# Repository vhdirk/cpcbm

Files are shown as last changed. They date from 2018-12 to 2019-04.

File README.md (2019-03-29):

## NOTE: All the files and informations in the mechanics folder of this repository are licensed under CC-BY-NC-SA license.

## Please, refer to the following link to know the details about this license.



## News[31-12-2018]: The complete release of the mechanical drawings of the machine are OUT!!! Informative videos will follow as soon as possible.

## Youtube Channel: [The Ant PCB Maker](https://www.youtube.com/channel/UCX44z-SSL7LzcB4xxgUdHHA)

## Instagram : [The Ant Team](https://www.instagram.com/the_ant_team/)

## Contact us at: the.ant.pcb@gmail.com or compact.pcb.maker.team@gmail.com

alternativetext (https://www.youtube.com/channel/UCX44z-SSL7LzcB4xxgUdHHA)

The Ant is a project to develop a CNC machine able to realize single and double-layered printed circuit boards.

[Here is a video presentation](https://youtu.be/nVkbG-CYaAA)

The CNC machine is designed to achieve well-determined characteristics:

- Compact
- Low-cost
- Robust
- Scalable
- Easy to build
- Open License

To achieve these properties the following design principle have been adopted:

- Electrical, mechanical and electronics parts have been chosen to be small, low-cost and easily available on the open market or 3D printable
- Mechanical design has been oriented to minimize the space occupied by the components
- Mechanics has been designed to be robust and stress resistant
- Mechanics has been designed so that the external dimensions of the machine may be changed with a minimal change of pieces and no re-design needed.
- Mechanical and electrical designs have taken in account the assembling and disassembling operations, allowing to use easily available tools as screwdrivers, Allen wrenches and a solder for electrical contacts.
- The microcontroller board used to control the CNC machine is inexpensive (~15 $) but is equipped with a powerful STM32 processor and many peripherals.
- The machine control firmware can be loaded with almost no effort, since the microcontroller board has been chosen to have an on-board programmer.
- The control firmware is derived from GRBL v.0.9j, but it is also customized to achieve better performance, taking advantage of the powerful processor, and to be more flexible, since more configuration parameters and features have been added respect to the original firmware

The Ant is an open project, but if you feel like donating a small sum, you are very welcome. Just use the paypal button below.

paypal (https://www.paypal.com/cgi-bin/webscr?cmd=_s-xclick&hosted_button_id=BTRCVPZUZYW2E)

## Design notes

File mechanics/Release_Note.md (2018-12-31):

# 31-12-2018

## Scope

Release of mechanical drawings of the Compact PCB Maker. 
This release completes the previous one and comprises the mechanical drawings of the bridge, of the head and of the microcontroller cover. 
The suggestions of the previous release apply also to this one.

# 09-12-2018

## Scope

First release of mechanical drawings of the Compact PCB Maker. 
This is a partial release that comprises all the frame related mechanical drawings. Other parts and corrections will follow in other releases.

## Suggestions

We suggest you to print the parts as they are, because the printing position is designed to enhance the mechanical behavior.

We also suggest you to print with a 0.2 mm layer thickness, 25% of infill, 1.5 mm of wall thickness and extrusion width (also called line width) of 0.5 mm.

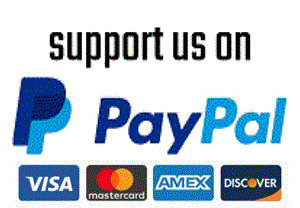
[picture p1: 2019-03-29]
resources/button/pp_button_small.gif

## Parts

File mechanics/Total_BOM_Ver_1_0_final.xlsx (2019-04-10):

Item | 1 | 2 | 3 | 4 | 5 | 6 | Qty | Info
Makerbeam - 10x10mm aluminum profile 200mm (black) | 8 |  |  |  |  |  | 8 | Makerbeam
Makerbeam - 10x10mm aluminum profile 60mm (black) | 4 |  |  |  |  |  | 4 | Makerbeam
Makerbeam - 10x10mm aluminum Right Angle bracket | 8 |  |  |  |  |  | 8 | Makerbeam
M3x6mm square headed bolt | 47 |  |  |  |  |  | 47 | Makerbeam
ISO 7380 M3X4 A2 | 8 |  |  |  | 4 |  | 12 | Makerbeam
Makerbeam T-slot nut | 24 |  |  |  |  |  | 24 | Makerbeam
M3 self-locking nut | 46 | 9 |  | 2 |  |  | 57
M3 nut | 4 |  |  |  |  | 8 | 12
M5 nut |  |  |  | 1 |  | 2 | 3
M2x8mm DIN 912 bolt |  |  |  |  | 2 |  | 2
M2.5x8mm DIN 912 bolt |  |  |  | 8 |  |  | 8
M3x6mm DIN 912 bolt | 12 | 9 |  | 2 | 3 |  | 26
M3x8mm DIN 912 bolt |  |  |  |  | 4 |  | 4
M3x10mm DIN 912 bolt |  | 4 |  |  |  | 8 | 12
M3x16mm DIN 912 Bolt | 2 |  |  |  | 4 |  | 6
M3x20mm DIN 912 Bolt | 8 |  |  | 1 |  |  | 9
M3x25mm DIN 912 bolt |  |  |  | 2 |  |  | 2
M3x30mm DIN 912 Bolt | 4 |  |  |  |  |  | 4
M3x50mm DIN 912 bolt |  | 2 |  |  | 4 |  | 6
M5x16mm hexagon head bolt |  |  |  |  |  | 2 | 2
Wood screws 3x16mm |  |  |  |  |  | 6 | 6
M3 locking Washer (internal diameter 3mm, external 5.5mm) | 8 | 14 |  |  |  |  | 22
M3 Washer (internal diameter 3mm, external 7.5mm) | 16 | 10 |  |  |  |  | 26
GT2 pulley 16T Bore 3mm with bearings | 4 | 2 |  |  |  |  | 6 | Aliexpress
GT2 pulley No Teeth Bore 3mm with bearings |  | 2 |  |  |  |  | 2 | Aliexpress
GT2 pulley 16T Bore 5mm height 10mm |  |  |  | 2 |  |  | 2 | Aliexpress
GT2 6mm Timing belt piece 100 cm |  |  |  | 2 |  |  | 2 | Aliexpress
Timing Belt Tensioner Spring | 2 |  |  |  |  |  | 2 | SKU135539-3 FFIO PCK
MGN9H Linear Rail 200 mm | 2 |  |  |  |  |  | 2 | Aliexpress or Banggood
Bearings lm6uu |  | 8 |  |  |  |  | 8 | Amazon
Bearing mochu 706C |  | 2 |  |  |  |  | 2 | Aliexpress
Chrome Plated Rods 6x180mm |  | 2 |  |  |  |  | 2 | Aliexpress (can be 6x200mm)
Chrome Plated Rods 6x100mm |  | 2 |  |  |  |  | 2
Threaded Rods M3x100mm |  | 3 |  |  |  |  | 3
Mechanical Limit Switch Module Vertical |  | 2 |  |  |  |  | 2 | Aliexpress
Mechanical endstop micro switch with dupont terminal |  |  | 1 |  |  |  | 1 | Aliexpress
ER8M-C6-60L chuck with 1/8" spring collect |  |  |  | 1 |  |  | 1 | Aliexpress
Lock collar(ring) internal diameter 6 mm, external diameter 12mm |  |  |  | 1 |  |  | 1 | Amazon or Aliexpress. The measured external diameter is 13mm
O-ring inner diameter 17mm, 1.78mm thick |  |  |  |  |  | 2 | 2
NEMA-11 JK28HS51-674 |  |  | 2 |  |  |  | 2 | Aliexpress or Banggood
Z axis motor LC1574W-04-025 |  |  |  | 1 |  |  | 1
M12 nut with step 1.75mm, 5mm thick |  |  |  | 1 |  |  | 1 | This should be sold with the Z-axis motor, if not use the correspondant 3D printed part.
2632 brushless outrunner motor 1000 kV |  |  | 1 |  |  |  | 1 | Turnigy on HobbyKing or Mistery on Aliexpress. The latter is still not tested and requires different head pieces
ESC AFRO 20A |  |  | 1 |  |  |  | 1 | HobbyKing
Nucleo F401RE |  |  |  |  | 1 |  | 1
CNC arduino shield V3 |  |  |  |  | 1 |  | 1
Stepstick stepper driver |  |  |  |  | 3 |  | 3
Male 3.5 bullet connectors |  |  | 3 |  |  |  | 3
Female 3.5mm bullet connectors |  |  | 2 |  |  |  | 2
Male JST connector |  |  | 1 |  |  |  | 1
Female Dupont connector 1x04 |  |  | 2 |  |  |  | 2
Female Dupont pin |  |  | 14 |  |  |  | 14
Female Dupont connector 1x03 |  |  | 2 |  |  |  | 2
Crocodile clips with plastic covers |  |  | 2 |  |  |  | 2
Extension Servo Lead Wire Male to Female 10 cm cable |  |  | 1 |  |  |  | 1
Stereo earphone with jack 3.5mm |  |  | 1 |  |  |  | 1
Cable 26 AWG about 40 cm |  |  | 4 |  |  |  | 4
Cable 16 AWG about 40 cm |  |  | 2 |  |  |  | 2
Cable 16AWG about 20cm |  |  |  |  | 2 |  | 2
Dupont cable Female to Female 20 cm |  |  |  |  | 2 |  | 2
Pieces of heat shrink tube |  |  |  |  |  |  |  | Various with different sizes
Small zip ties |  |  |  | 4 |  |  | 4
2.54mm jumper |  |  |  |  | 10 |  | 10
Sheath spiral tube 6 mm about 1 m |  |  |  |  | 1 |  | 1
MDF wood board 240x150x10mm (LxWxH) |  |  |  | 1 |  |  | 1
12V on-off round switch with 14mm mounting hole |  |  |  |  | 1 |  | 1
Panel mount DC power jack inner diameter 2.5mm external diameter 5.5mm |  |  |  |  | 1 |  | 1
Panel mount 3.5mm mono female headphone plug |  |  |  |  | 1 |  | 1
12V brushless 40x40x10mm fan |  |  |  |  | 1 |  | 1
12V 10A power supply |  |  |  |  |  | 1 | 1

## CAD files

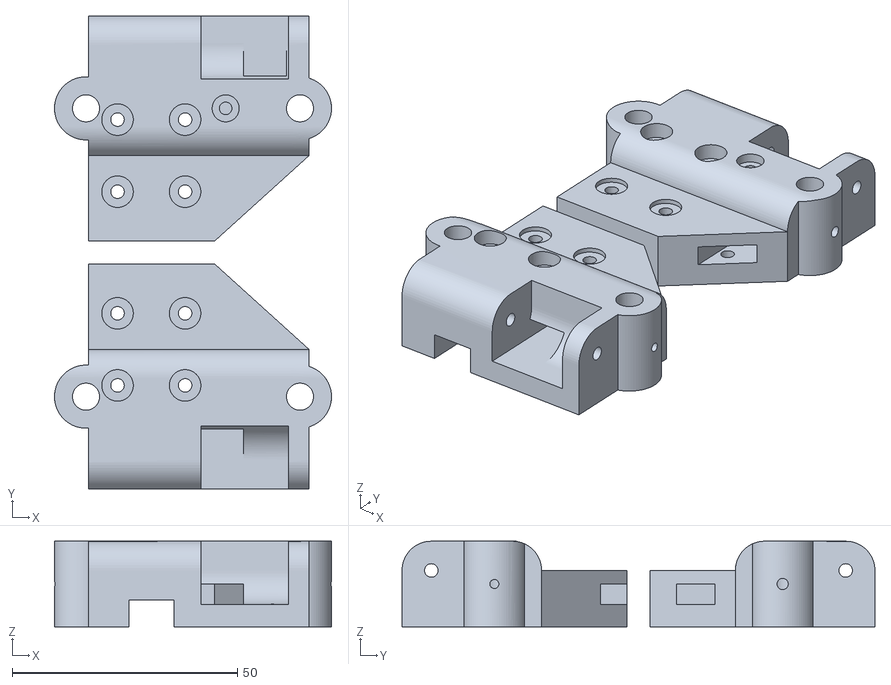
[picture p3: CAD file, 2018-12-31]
mechanics/bridge/bridge_right_and_left_1p2.stl
61.5 x 105.0 x 19.0

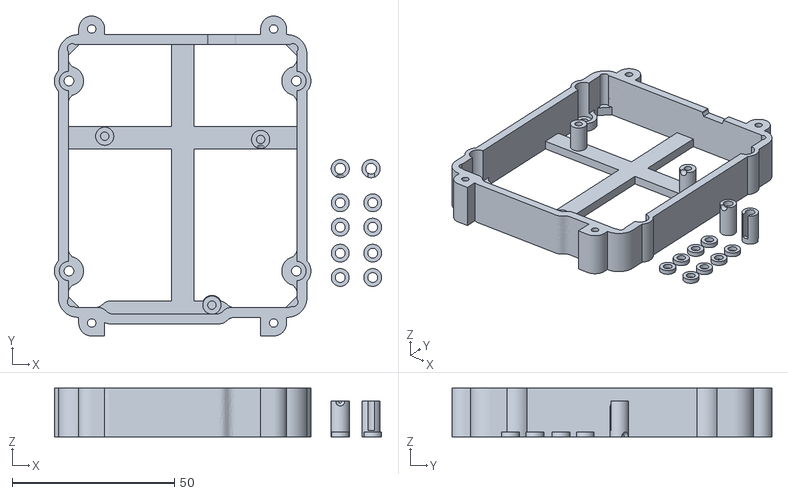
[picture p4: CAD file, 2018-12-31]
mechanics/electronics_and_accessories/nucleo_back_1p4.stl
100.8 x 98.5 x 15.0

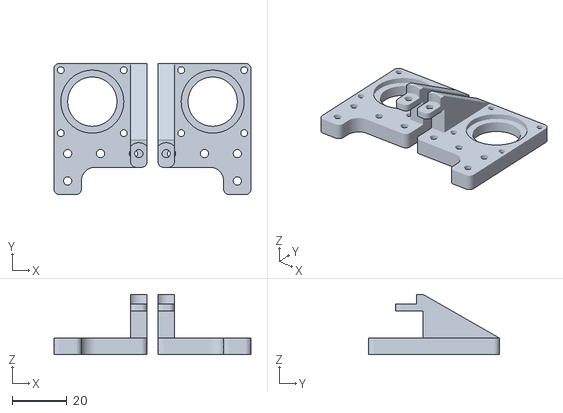
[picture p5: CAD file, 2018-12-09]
mechanics/frame/motor_holder_1p0.stl
72.0 x 48.0 x 22.0

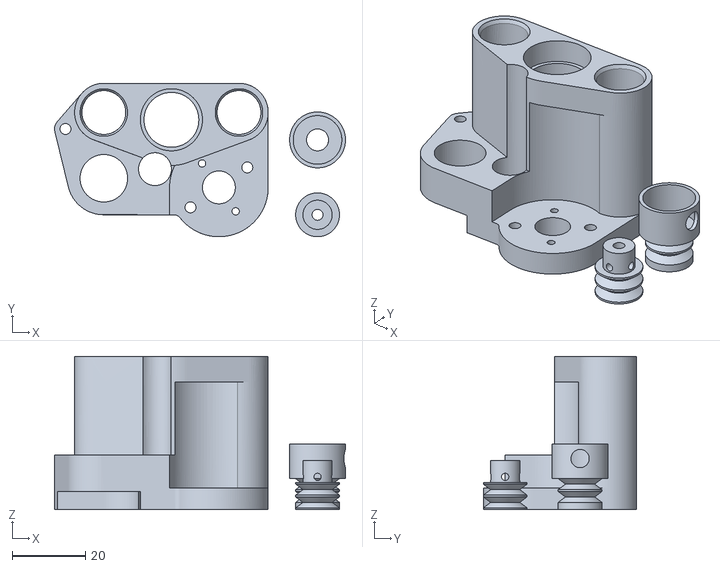
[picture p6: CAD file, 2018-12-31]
mechanics/head/head_4p0.stl
79.7 x 42.0 x 42.0

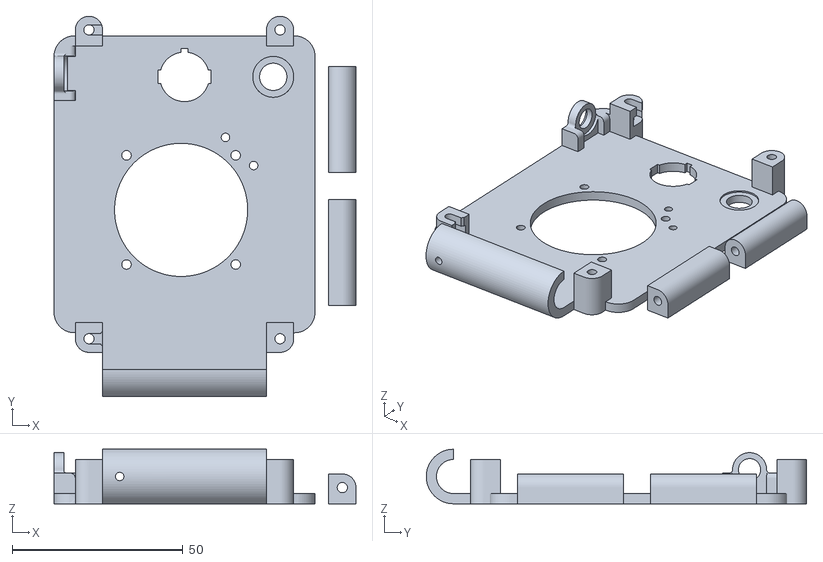
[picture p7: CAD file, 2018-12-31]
mechanics/electronics_and_accessories/nucleo_cover_1p4.stl
88.5 x 111.5 x 16.0

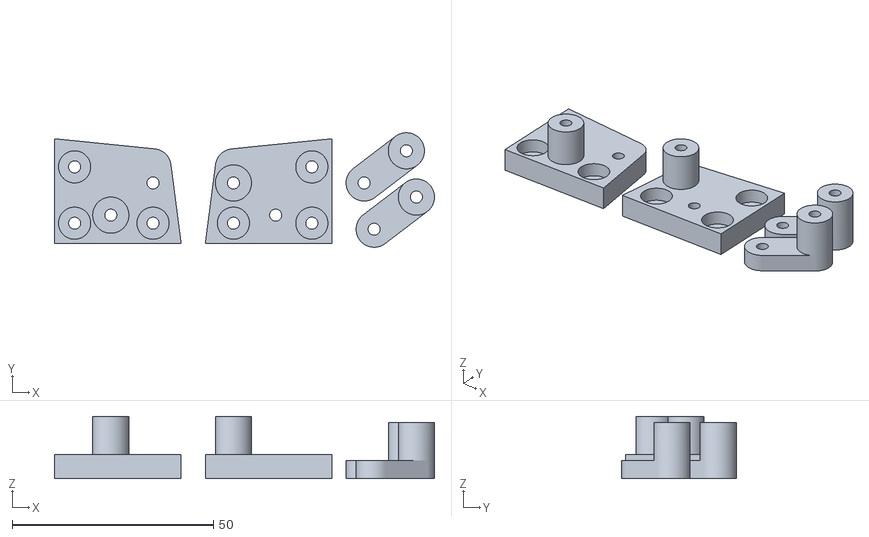
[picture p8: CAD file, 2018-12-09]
mechanics/frame/GT2_pulley_support_1p0.stl
94.5 x 28.5 x 15.5

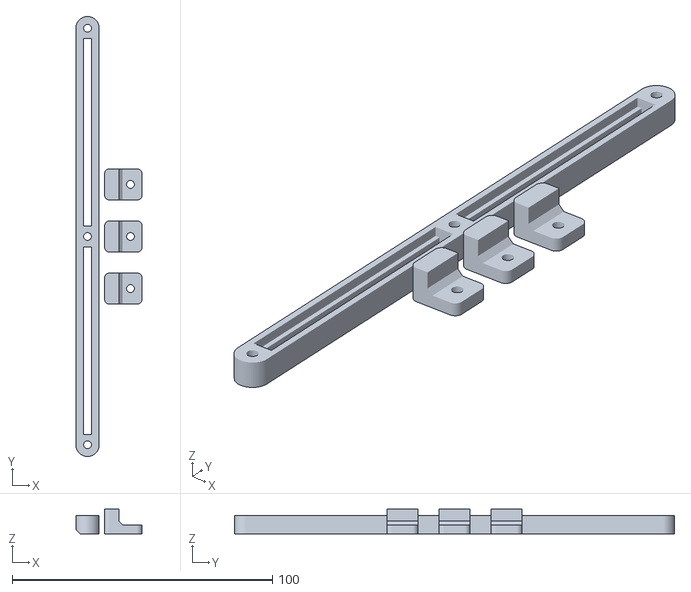
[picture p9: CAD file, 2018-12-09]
mechanics/frame/pcb_lock_1p0.stl
25.5 x 169.0 x 9.50

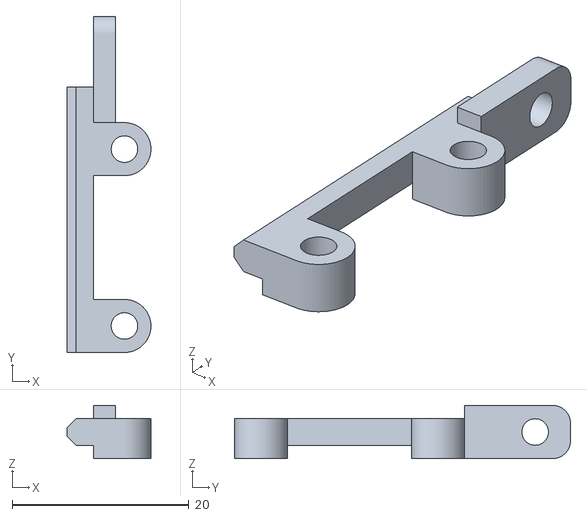
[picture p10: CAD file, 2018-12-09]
mechanics/frame/limit_y_support_1p0.stl
9.50 x 38.0 x 6.00

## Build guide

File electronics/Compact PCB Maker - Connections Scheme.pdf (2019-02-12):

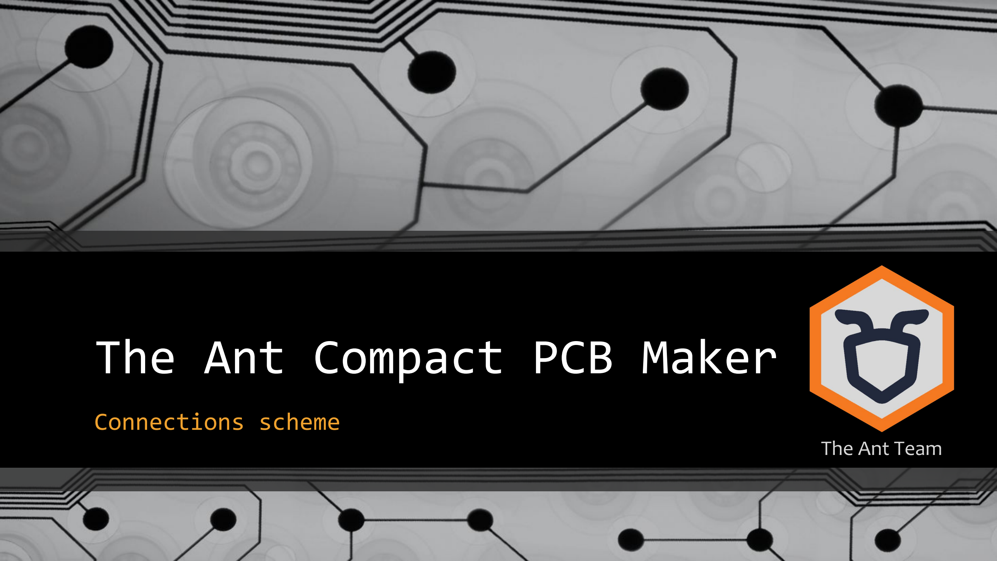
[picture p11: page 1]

# The Ant Compact PCB Maker

### Connections scheme

The Ant Team

# Introduction

## This document shows how to connect the different electronics parts of The Ant Machine. We strongly suggests you to watch this video:

## https://youtu.be/eRefCvD_KVs

as a preparation for this stage of machine construction.

# Electronics central unit parts

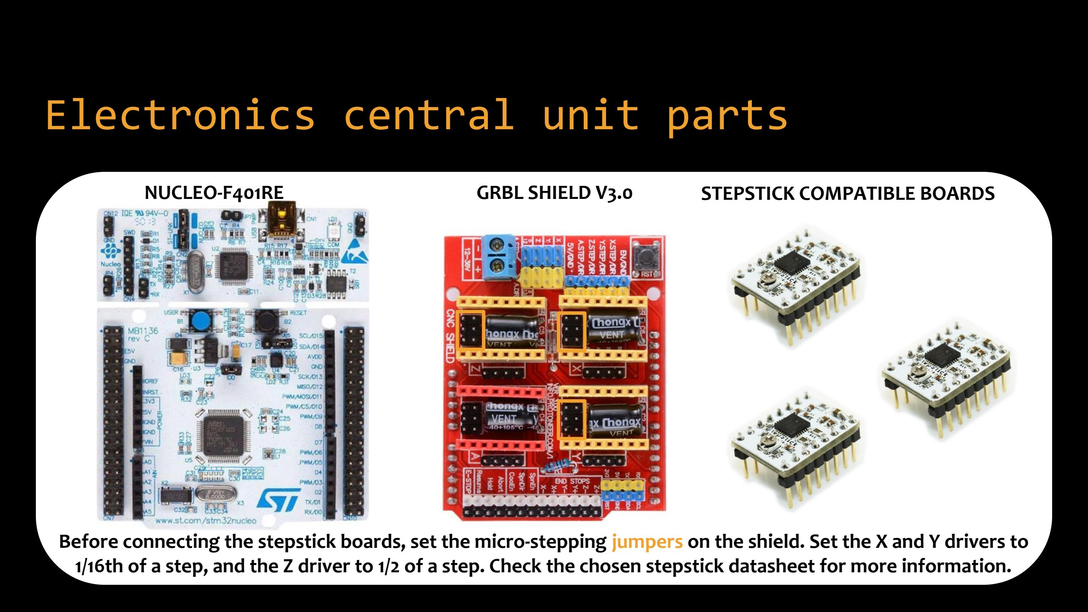
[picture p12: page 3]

Before connecting the stepstick boards, set the micro-stepping jumpers on the shield. Set the X and Y drivers to 1/16th of a step, and the Z driver to 1/2 of a step. Check the chosen stepstick datasheet for more information.

NUCLEO-F401RE | GRBL SHIELD V3.0 | STEPSTICK COMPATIBLE BOARDS

# Power Supply

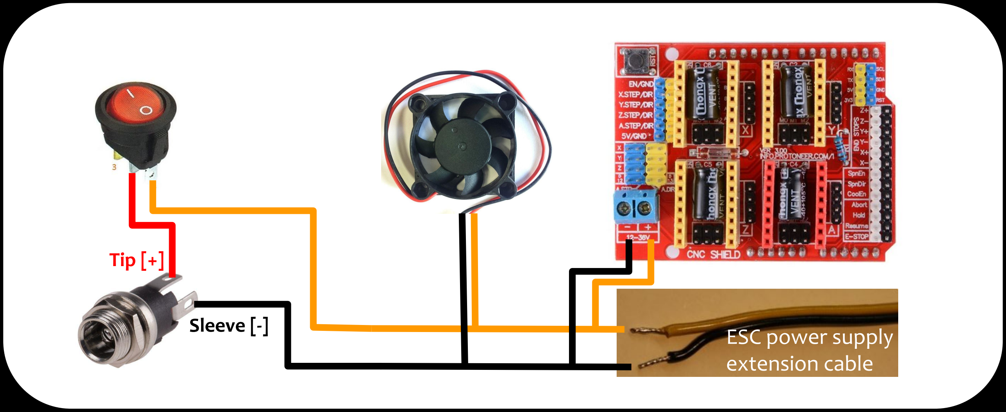
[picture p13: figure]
ESC power supply extension cable; Sleeve [-]; Tip [+]

# ESC Power Supply

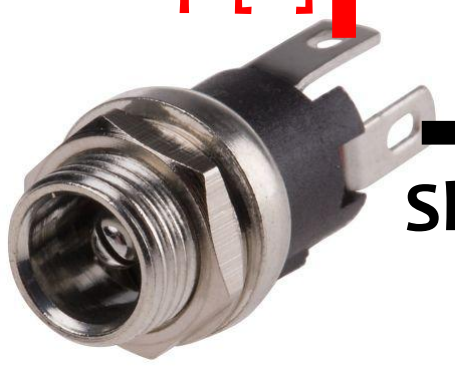
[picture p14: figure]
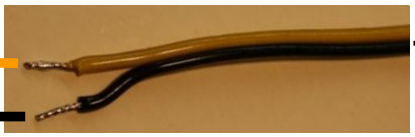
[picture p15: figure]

Sleeve [-]

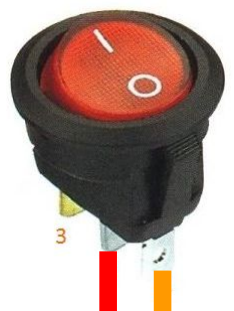
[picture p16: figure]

Tip [+]

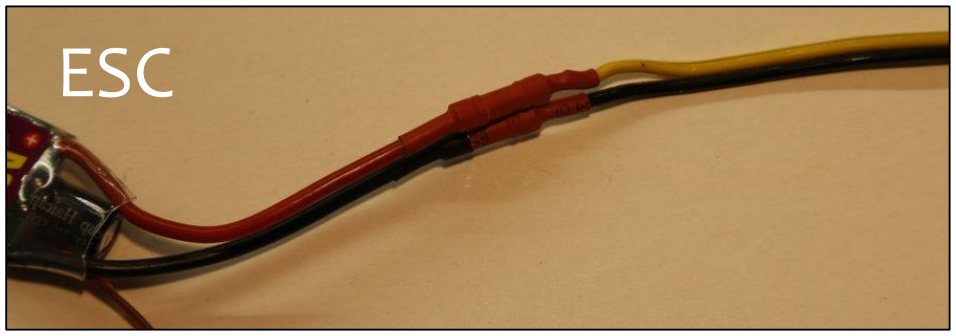
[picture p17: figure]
ESC

# CoreXY Stepper Motors

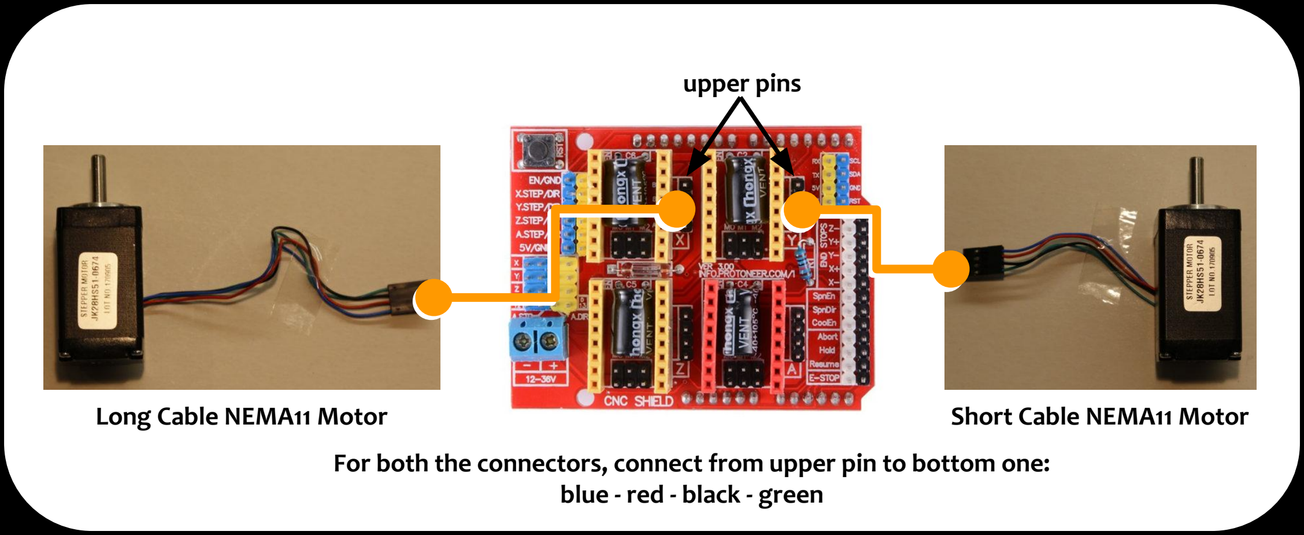
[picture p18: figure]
blue - red - black - green; upper pins; Long Cable NEMA11 Motor; Short Cable NEMA11 Motor

For both the connectors, connect from upper pin to bottom one:

# Z axis Stepper Motor

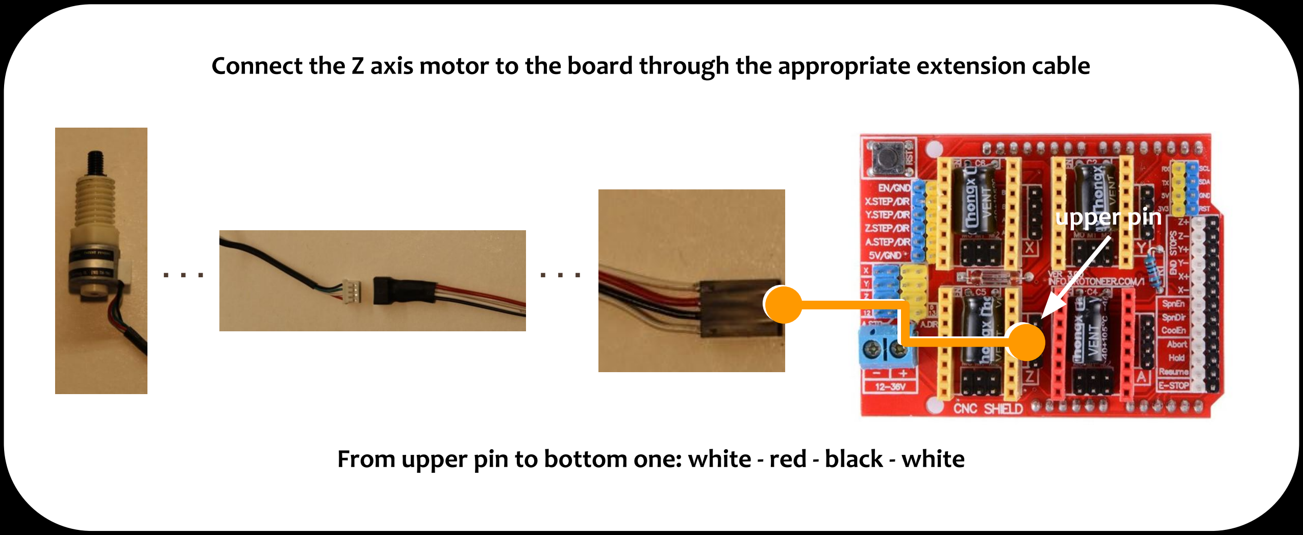
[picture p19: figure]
upper pin

From upper pin to bottom one: white - red - black - white

Connect the Z axis motor to the board through the appropriate extension cable

# Z axis Limit Switch

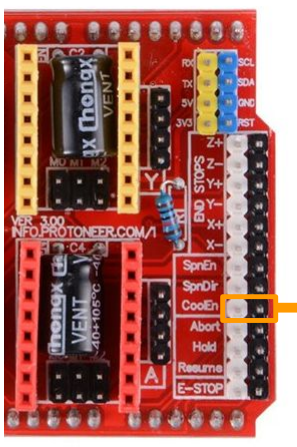
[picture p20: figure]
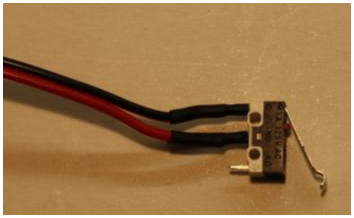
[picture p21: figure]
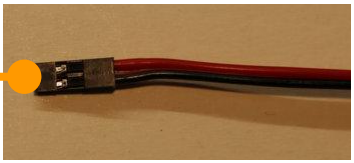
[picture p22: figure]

Black ground wire connected to the right pin, signal red wire connected to the left pin

# Y axis Limit Switch

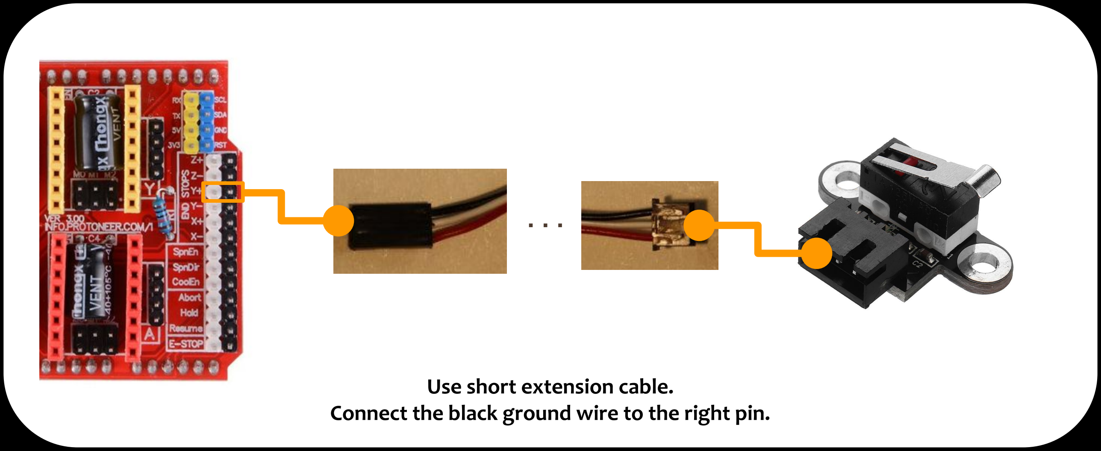
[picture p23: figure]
Use short extension cable.

Connect the black ground wire to the right pin.

# X axis Limit Switch

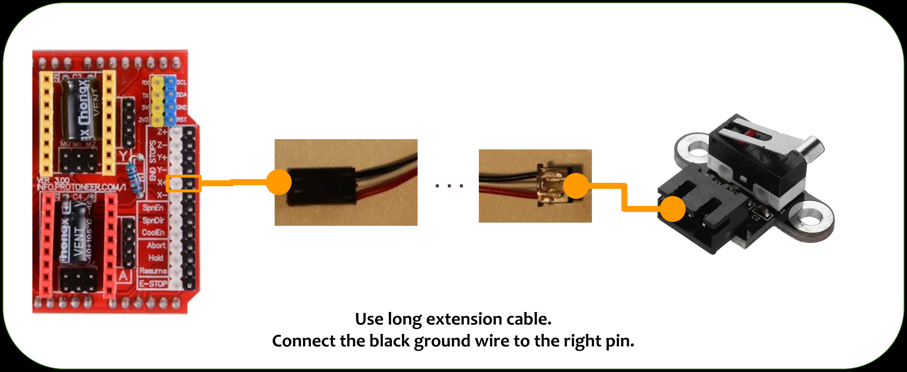
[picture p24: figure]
Use long extension cable.

Connect the black ground wire to the right pin.

# Spindle PWM control

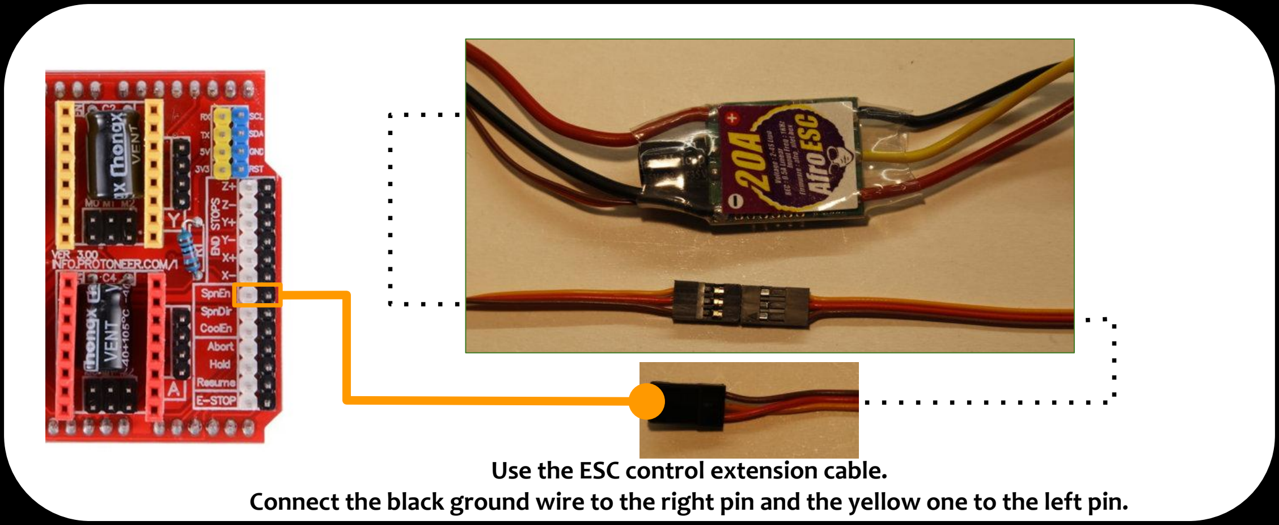
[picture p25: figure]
Use the ESC control extension cable.

Connect the black ground wire to the right pin and the yellow one to the left pin.

# Spindle ESC to brushless

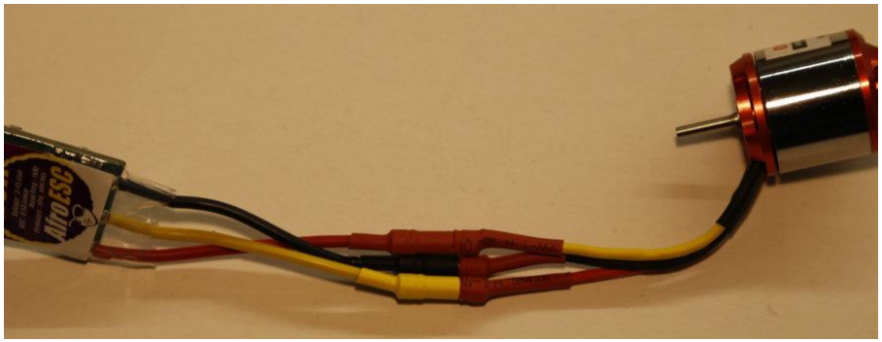
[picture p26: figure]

Check the connections. Red and Yellow wire must be inverted.

# Probe jack connector

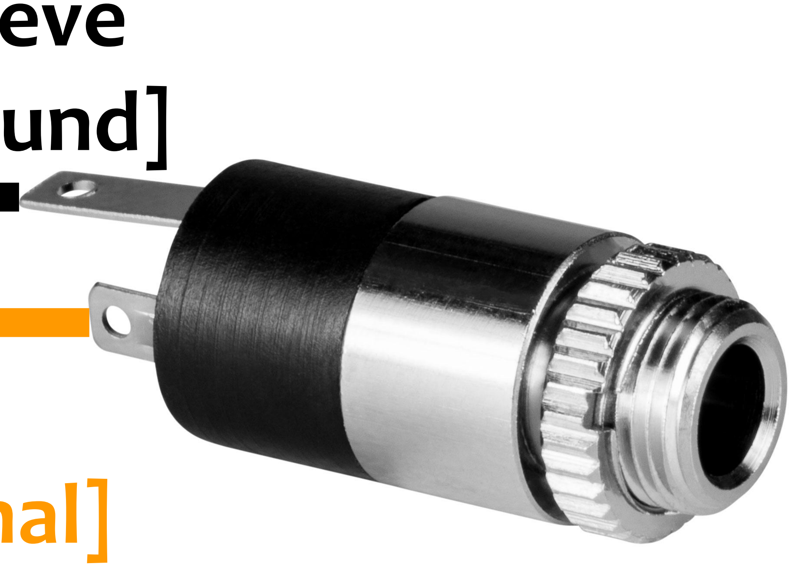
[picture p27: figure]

Sleeve
[ground]

Tip
[probe signal]

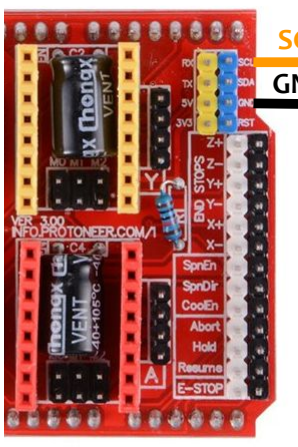
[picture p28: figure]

SCL
GND

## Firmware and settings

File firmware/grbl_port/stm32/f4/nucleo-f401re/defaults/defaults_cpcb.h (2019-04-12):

/*
  defaults_cpcb.h - defaults settings configuration file for Compact PCB Maker machine.
  Part of grbl_port_opencm3 project.

  Copyright (c) 2017 Angelo Di Chello

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
  You should have received a copy of the GNU General Public License
  along with Grbl_port_opencm3.  If not, see <http://www.gnu.org/licenses/>.
*/

/* The defaults.h file serves as a central default settings file for different machine
   types, from DIY CNC mills to CNC conversions of off-the-shelf machines. The settings
   here are supplied by users, so your results may vary. However, this should give you
   a good starting point as you get to know your machine and tweak the settings for your
   nefarious needs. */


//#ifndef GRBL_PORT_STM32_F4_NUCLEO_F401RE_GRBL_DEFAULTS_DEFAULTS_CPCB_H_
//#define GRBL_PORT_STM32_F4_NUCLEO_F401RE_GRBL_DEFAULTS_DEFAULTS_CPCB_H

#ifndef defaults_h
#define defaults_h

  // Grbl generic default settings. Should work across different machines.
  #define DEFAULT_X_STEPS_PER_MM 100.0
  #define DEFAULT_Y_STEPS_PER_MM 100.0
  #define DEFAULT_Z_STEPS_PER_MM 100.0
  #define DEFAULT_X_MAX_RATE 1000.0 // mm/min
  #define DEFAULT_Y_MAX_RATE 1000.0 // mm/min
  #define DEFAULT_Z_MAX_RATE 500.0 // mm/min
  #define DEFAULT_X_ACCELERATION (10.0*60*60) // 10*60*60 mm/min^2 = 10 mm/sec^2
  #define DEFAULT_Y_ACCELERATION (10.0*60*60) // 10*60*60 mm/min^2 = 10 mm/sec^2
  #define DEFAULT_Z_ACCELERATION (10.0*60*60) // 10*60*60 mm/min^2 = 10 mm/sec^2
  #define DEFAULT_X_MAX_TRAVEL 200.0 // mm
  #define DEFAULT_Y_MAX_TRAVEL 200.0 // mm
  #define DEFAULT_Z_MAX_TRAVEL 200.0 // mm
  #define DEFAULT_STEP_PULSE_MICROSECONDS 10
  #define DEFAULT_STEPPING_INVERT_MASK 0
  #define DEFAULT_DIRECTION_INVERT_MASK 0
  #define DEFAULT_STEPPER_IDLE_LOCK_TIME 255 // msec (0-254, 255 keeps steppers enabled)
  #define DEFAULT_STATUS_REPORT_MASK ((BITFLAG_RT_STATUS_MACHINE_POSITION)|(BITFLAG_RT_STATUS_WORK_POSITION))
  #define DEFAULT_JUNCTION_DEVIATION 0.01 // mm
  #define DEFAULT_ARC_TOLERANCE 0.002 // mm
  #define DEFAULT_REPORT_INCHES 0 // false
  #define DEFAULT_INVERT_ST_ENABLE 0 // false
  #define DEFAULT_INVERT_LIMIT_PINS 0 // false
  #define DEFAULT_SOFT_LIMIT_ENABLE 0 // false
  #define DEFAULT_HARD_LIMIT_ENABLE 1  // false
  #define DEFAULT_HOMING_ENABLE 1  // true
  #define DEFAULT_HOMING_DIR_MASK 0 // move positive dir
  #define DEFAULT_HOMING_FEED_RATE 25.0 // mm/min
  #define DEFAULT_HOMING_SEEK_RATE 500.0 // mm/min
  #define DEFAULT_HOMING_DEBOUNCE_DELAY 250 // msec (0-65k)
  #define DEFAULT_HOMING_PULLOFF 1.0 // mm

#endif /* GRBL_PORT_STM32_F4_NUCLEO_F401RE_GRBL_DEFAULTS_DEFAULTS_CPCB_H */

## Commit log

2016-02-14 Demo driver and others examples with libopencm3 and Nucleo F401.
2016-02-16 Removed unused targets. Added a test with timer2 that blinks a the user led.
2016-04-10 Added simple test of linked timers.
2016-08-02 Grbl import draft.
    [config.h]
2016-08-09 testing stepper porting on nucleo f401
    [config.h, cpu_map.h, defaults.h]
2016-08-19 starting grbl porting
    [config.h, cpu_map.h, defaults.h]
2016-08-21 Adding print and report (still ongoing)
2016-12-09 Added test routines for inputs on nucleo
    [config.h]
2016-12-11 Corrections on inputs management.
    [config.h]
2017-01-15 First draft for flash erase on if'-needed basis.
    [config.h]
2017-02-27 Draft of memory management (still ongoing)
    [config.h]
2017-03-06 Adding other parts (spindle and coolant stubbed at the moment)
2017-03-15 adding missing files and functions.
    [main.c]
2017-06-28 Delay functions based on SysTick.
    [config.h]
2017-06-30 Initial part of modification for spindle control.
2017-06-30 spindle_control.c edited online with Bitbucket
2017-07-03 Modification on limit Z pin configuration and exti0 used as limit Z interrupt.
2017-07-09 Correction of delay functions and first corrections of spindle control settings.
2017-07-13 PWM spindle working (first test).
2017-07-19 Correcting timer period and changing pwm mode from 2 to 1 (upcounting, 1 if less, 0 if more).
2017-09-11 Probe input set on PC4 GPIO.
    [config.h]
2017-09-12 Adding missing call to probe_state_monitor function.
2017-09-12 Probe moved to its original position PC0.
2017-09-19 Lowered main interrupt priority, with preemption. Allows UART interrupt to be served on time.
2017-10-02 Correction to adapt to new libraries.
    [config.h]
2017-10-02 Eliminated unuseful files. Added Debug configuration file for TrueStudio.
    [config.h, cpu_map.h, defaults.h]
2017-10-15 Solved stalling cpu issue. Serial RX uses DMA as a default.
2017-10-18 File license headers updated.
    [config.h, cpu_map.h]
2017-10-20 Build aligned to last grbl 0.9 build (26-07-2016). Inserted coolant control pins and functions.
    [config.h, cpu_map.h]
2017-11-27 Align repo after prototype test.
    [config.h, cpu_map.h, defaults.h]
2018-01-22 Variable pwm spindle made parametric. First issue.
2018-02-19 CPCB default: keep stepper enabled.
2018-02-19 Adding default pwm spindle parameters.
    [config.h]
2018-02-23 Repo aligned to grbl_open_cm3 structure.
2018-04-14 Correction of S0. The minimum spindle value should be set
2018-04-25 COREXY manages the direction pin inversion in the planning to avoid single motor direction inversion. Added implicit build info. INVERT_LIMIT_PIN_MASK disabled.
2018-04-30 Steps calculation corrected for COREXY. HOMING order is now Z Y X.
2018-05-12 Homing first correction, test led re-added. Default homing changed for CPCB.
2018-05-13 Homing final correction.
2018-05-13 Using just one function to set debounce timer.
2018-08-12 Added parameter that allows to enable the spindle with minimal RPM at startup.
2018-09-08 Redundant probe check to filter glitches.
2018-12-09 First mechanical drawings partial release
    [GT2_pulley_support_1p0.stl, limit_y_support_1p0.stl, motor_holder_1p0.stl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]
2018-12-22 Moved frame parts in a dedicated folder [skip ci]
    [GT2_pulley_support_1p0.stl, limit_y_support_1p0.stl, motor_holder_1p0.stl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]
2018-12-31 Mechanical drawings release
    [bridge_right_and_left_1p2.stl, head_4p0.stl, nucleo_back_1p4.stl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]
2019-01-12 Correcting homing failure bug. Removed compilation warning.
2019-03-19 Added partial bom per frame video [skip ci].
2019-03-19 Added partial bom for bridge and head video [skip ci].
2019-03-21 Partial Bridge and HEad BOM vertical-horizontal limit switch correction.
2019-03-26 Added Total BOM version 1.0.
    [Total_BOM_Ver_1_0_final.xlsx]
2019-04-02 Small adjustments to BOM.
    [Total_BOM_Ver_1_0_final.xlsx]
2019-04-10 Fixing typo [skip ci]
    [Total_BOM_Ver_1_0_final.xlsx]
2019-04-12 Correction: Added default parameters for AFRO 20 ESC spindle and X DIRECTION mask set to 0.
    [defaults_cpcb.h, pwm_spindle_params_afro20.h]

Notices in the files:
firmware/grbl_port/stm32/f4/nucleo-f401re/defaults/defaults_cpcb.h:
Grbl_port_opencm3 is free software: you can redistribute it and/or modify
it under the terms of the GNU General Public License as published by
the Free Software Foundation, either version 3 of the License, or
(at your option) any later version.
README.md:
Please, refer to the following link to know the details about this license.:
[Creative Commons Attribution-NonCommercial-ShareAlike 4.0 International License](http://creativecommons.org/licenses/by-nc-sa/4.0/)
